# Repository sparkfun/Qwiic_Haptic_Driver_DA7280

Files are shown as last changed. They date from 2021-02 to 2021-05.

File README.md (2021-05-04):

SparkFun Qwiic Haptic Driver - DA7280
========================================

<table class="table table-hover table-striped table-bordered">
  <tr align="center">
   <td><a href="https://www.sparkfun.com/products/17590">*SparkFun Qwiic Haptic Driver - DA7280 (ROB-17590)</a></td>
   <td><a href="https://www.sparkfun.com/products/18247">SparkFun Qwiic Haptic Driver - DA7280 (ROB-18247)</a></td>
  </tr>
  <tr align="center">
   <td><i>SparkFun Qwiic Haptic Driver - DA7280 [<a href="https://www.sparkfun.com/products/17590">ROB-17590</a>]</i></td>
   <td><i>SparkFun Qwiic Haptic Driver Kit - DA7280 [<a href="https://www.sparkfun.com/products/18247">ROB-18247</a>]</i></td>
  </tr>
</table>

The SparkFun Qwiic Haptic Driver includes an itty-bitty, Linear Resonant Actuator (LRA) vibration motor and Dialog Semiconductor's DA7280 motor driver IC for applications that require haptic feedback. The kit is intended for applications where the vibration motor needs to be mounted separately from the board. Please be aware that you will need to manually solder the wires and motor to the board.

Control the vibration motor with the DA7280 via I<sup>2</sup>C, PWM, or a combination of three general purpose input pins. Utilizing our handy Qwiic system, no soldering is required to connect it to the rest of your system. However, we still include 0.1"-spaced PTH pads in case you prefer to use a breadboard to access the driver's I<sup>2</sup>C, power, interrupt, and general purpose input pins on the edge of the board.

This board is great for projects that require a physical indicator whenever an event is triggered. Add it to your remote control to notify you when your robot has hit a wall. Combine it with an accelerometer to remind you to correct your posture. Or use it with a distance sensor to alert you when a ninja is walking up to you at your desk.

Repository Contents
-------------------

* **/Documentation** - Data sheets, additional product information
* **/Hardware** - Eagle design files (.brd, .sch)
* **/Production** - Production panel files (.brd)

Documentation
--------------

* **[Library](https://github.com/sparkfun/DA7280_Haptic_Driver_Arduino_Library)** - Arduino library
* **[Hookup Guide](https://learn.sparkfun.com/tutorials/1461)**

Product Versions
----------------

* [ROB-17590](https://www.sparkfun.com/products/17590)

Version History
---------------

* v1.0 - Initial Release

License Information
-------------------

This product is _**open source**_! 

Please review the LICENSE.md file for license information. 

If you have any questions or concerns on licensing, please contact technical support on our [SparkFun forums](https://forum.sparkfun.com/viewforum.php?f=152).

Distributed as-is; no warranty is given.

- Your friends at SparkFun.

_<COLLABORATION CREDIT>_

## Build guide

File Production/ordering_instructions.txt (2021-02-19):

panel size, 143x192mm
PCB thickness, 1.6mm
number of layers, 2
soldermask color, Red
silkscreen color, White
oz copper, 1oz
finish, HASL lead free
stencils, top
pcs per panel, 30
min trace width, 0.2032mm / 0.0080in
min drill size, 0.3048mm / 0.0120in

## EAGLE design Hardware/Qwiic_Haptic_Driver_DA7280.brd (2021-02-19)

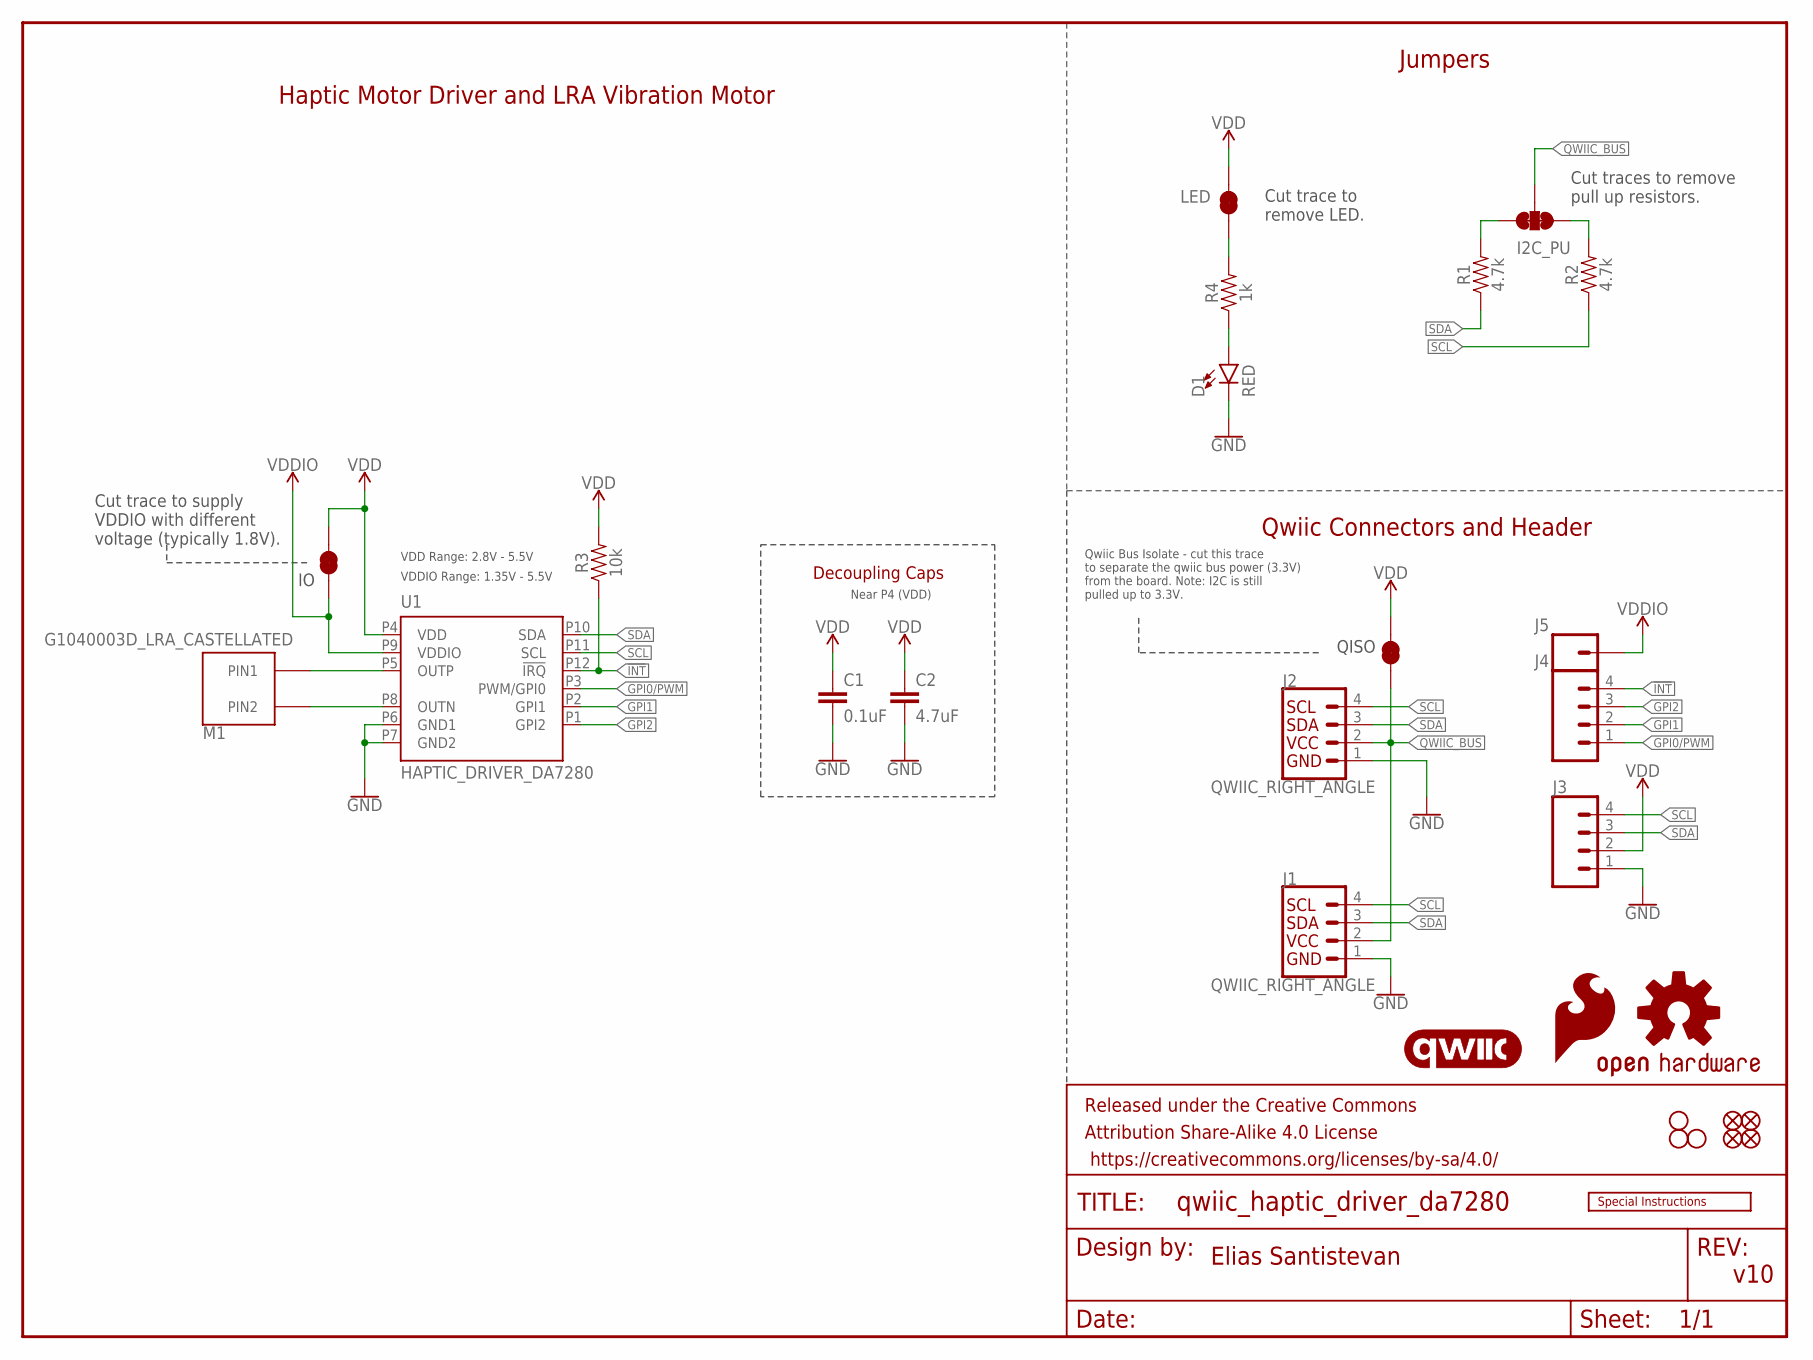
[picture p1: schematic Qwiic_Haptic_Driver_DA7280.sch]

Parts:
C1: 0.1uF; 0603
C2: 4.7uF; 0603
D1: RED; LED-0603
FD1, FD2, FD3, FD4: FIDUCIALUFIDUCIAL; FIDUCIAL-MICRO
FRAME1: FRAME-LETTER; CREATIVE_COMMONS
H1, H2, H4: STAND-OFFTIGHT; STAND-OFF-TIGHT
J1, J2: QWIIC_RIGHT_ANGLE; JST04_1MM_RA
J3, J4: CONN_041X04_NO_SILK_NO_POP; 1X04_NO_SILK
J5: CONN_01PTH_NO_SILK_YES_STOP; 1X01_NO_SILK
JP1, JP2, JP4: LED; SMT-JUMPER_2_NC_TRACE_SILK
JP3: I2C_PU; SMT-JUMPER_3_2-NC_TRACE_SILK
LOGO1: SPECIAL_INSTRUCTIONS-ORDERING; ORDERING_INSTRUCTIONS
LOGO2: OSHW-LOGOS; OSHW-LOGO-S
LOGO4: SFE_LOGO_FLAME.1_INCH; SFE_LOGO_FLAME_.1
M1: G1040003D_LRA_CASTELLATED; COIN_VIBRATION_MOTOR_CASTEL
R1, R2: 4.7k; 0603
R3: 10k; 0603
R4: 1k; 0603
U1: HAPTIC_DRIVER_DA7280; QFN_DA7280
U$1: QWIIC_LOGO_3MM; QWIIC_3MM

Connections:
!INT!: J4.4, R3.1, U1.P12 (!IRQ!)
GND: C1.2, C2.2, D1.C, J1.1, J2.1, J3.1, U1.P6 (GND1), U1.P7 (GND2)
GPI0/PWM: J4.1, U1.P3 (PWM/GPI0)
GPI1: J4.2, U1.P2 (GPI1)
GPI2: J4.3, U1.P1 (GPI2)
unnamed: D1.A, R4.1
unnamed: JP1.1, R4.2
unnamed: JP3.3, R1.2
unnamed: JP3.1, R2.2
unnamed: M1.P$1 (PIN1), U1.P5 (OUTP)
unnamed: M1.P$2 (PIN2), U1.P8 (OUTN)
QWIIC_BUS: J1.2, J2.2, JP3.2, JP4.1
SCL: J1.4, J2.4, J3.4, R2.1, U1.P11 (SCL)
SDA: J1.3, J2.3, J3.3, R1.1, U1.P10 (SDA)
VDD: C1.1, C2.1, J3.2, JP1.2, JP2.2, JP4.2, R3.2, U1.P4 (VDD)
VDDIO: J5.1, JP2.1, U1.P9 (VDDIO)

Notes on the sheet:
v10
Qwiic Connectors and Header
Jumpers
Cut trace to remove LED.
Cut traces to remove pull up resistors.
Haptic Motor Driver and LRA Vibration Motor
Elias Santistevan
Near P4 (VDD)
Decoupling Caps
VDD Range: 2.8V - 5.5V
VDDIO Range: 1.35V - 5.5V
Cut trace to supply VDDIO with different voltage (typically 1.8V).
QISO
Qwiic Bus Isolate - cut this trace to separate the qwiic bus power (3.3V) from the board. Note: I2C is still pulled up to 3.3V.

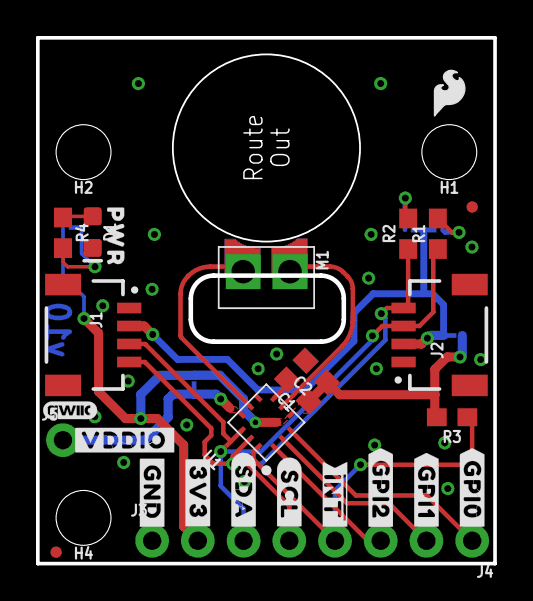
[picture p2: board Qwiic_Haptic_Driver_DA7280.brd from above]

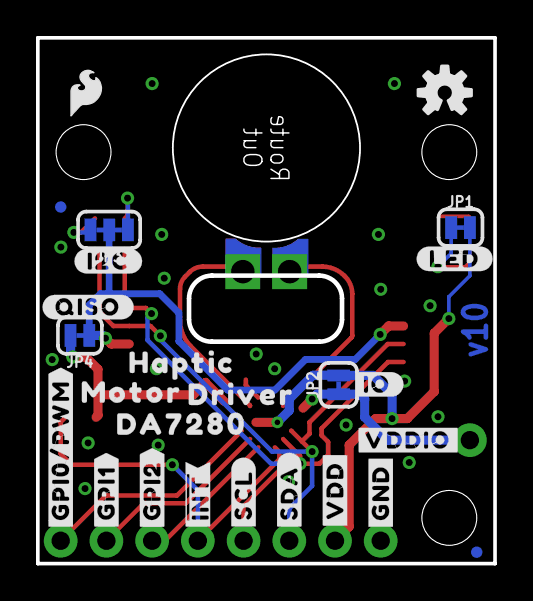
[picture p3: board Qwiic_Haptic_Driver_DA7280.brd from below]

Board: 2 copper layers, 25.4 x 29.2 mm, 58 parts (25 on the bottom side), 16 nets.

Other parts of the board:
U$2: #3V3#1
U$3, U$18: #GND#0
U$4: #GPI0#6
U$5: #GPI1#6
U$6: #GPI2#6
U$7: #VDD#4
U$8: #SDA#4
U$9: HAPTIC6
U$10: MOTOR7
U$11: DRIVER8
U$12: #GPI0#PWM#2
U$13: #GPI1#2
U$14: #GPI2#2
U$15, U$25: #VDDIO#5
U$16: #SDA#0
U$19: #SCL#5
U$20: PWR72810
U$21: #SCL#1
U$23: #I2C#4
U$24: #LED#4
U$26: SFE_LOGO_FLAME_.1
U$27: ##INT##3
U$28: ##INT##6
U$29: DA72809
U$30: #IO#6
U$31: #QISO#0

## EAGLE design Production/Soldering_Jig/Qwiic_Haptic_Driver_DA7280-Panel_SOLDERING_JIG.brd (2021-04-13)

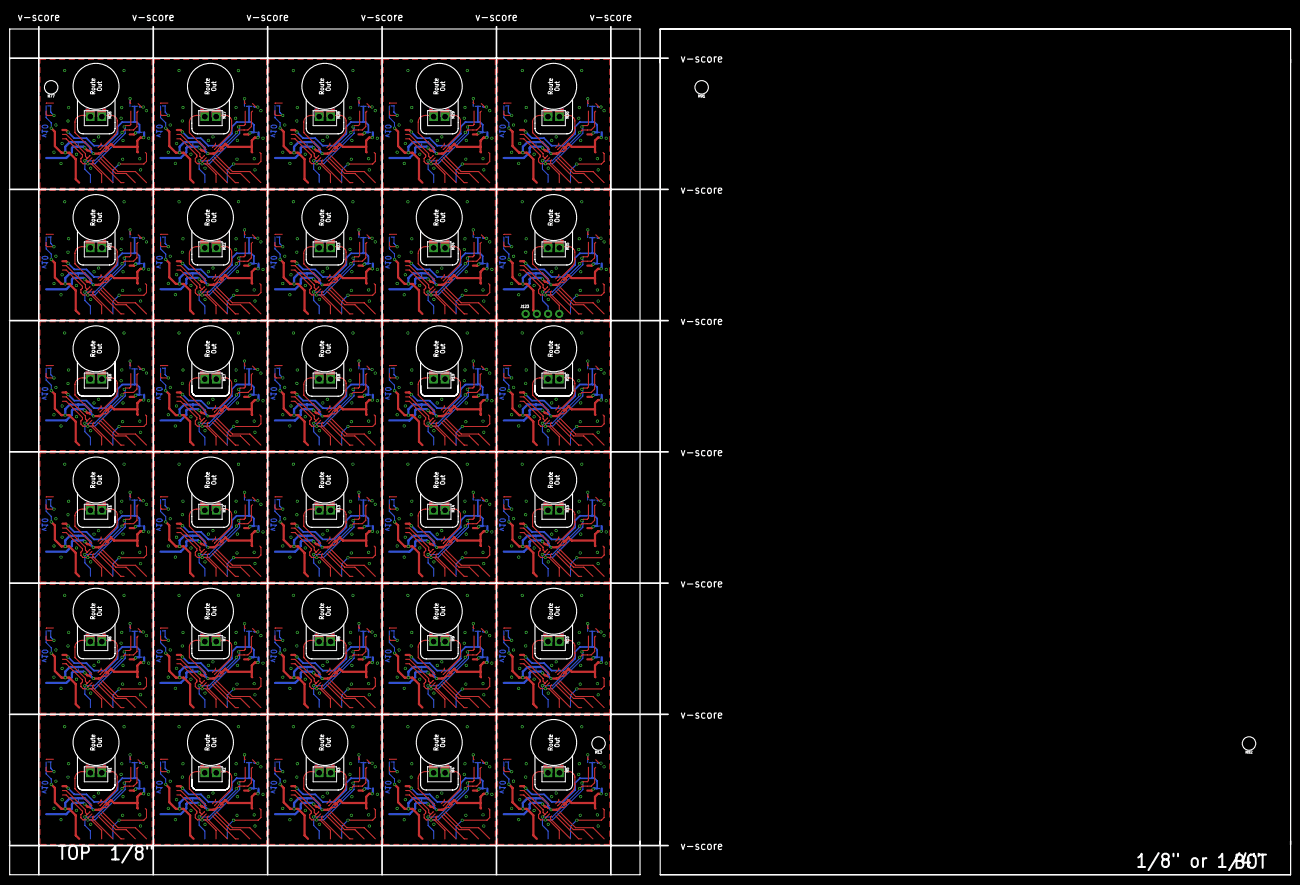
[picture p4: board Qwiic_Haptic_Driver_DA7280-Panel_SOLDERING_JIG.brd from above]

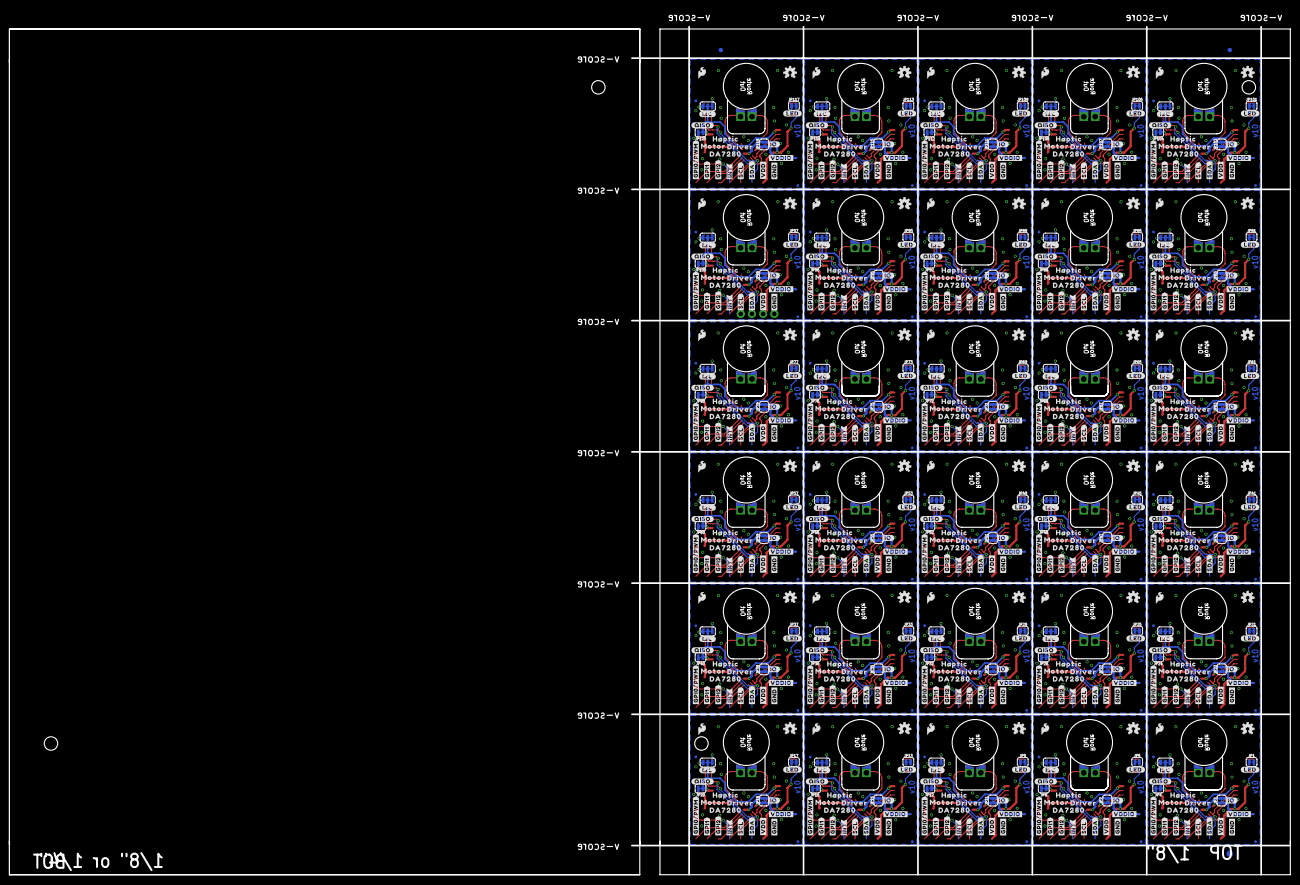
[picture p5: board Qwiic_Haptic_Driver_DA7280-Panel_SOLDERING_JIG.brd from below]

Board: 2 copper layers, 290.1 x 192.0 mm, 788 parts (753 on the bottom side), 60 nets.

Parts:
E$2, E$4: FIDUCIAL-1X2
E$6: FIDUCIAL-1.5X3
FD2, FD4, FD6, FD8, FD10, FD12, FD14, FD16, FD18, FD20, FD22, FD24, FD26, FD28, FD30, FD32, FD34, FD36, FD38, FD40, FD42, FD44, FD46, FD48, FD50, FD52, FD54, FD56, FD58, FD60, FD62, FD64, FD66, FD68, FD70, FD72, FD74, FD76, FD78, FD80, FD82, FD84, FD86, FD88, FD90, FD92, FD94, FD96, FD98, FD100, FD102, FD104, FD106, FD108, FD110, FD112, FD114, FD116, FD118, FD120: FIDUCIALUFIDUCIAL; FIDUCIAL-MICRO
H13, H77, H91, H92: STAND-OFFTIGHT; STAND-OFF-TIGHT
J123: 1X04_NO_SILK
JP1, JP2, JP4, JP5, JP7, JP8, JP9, JP11, JP12, JP13, JP15, JP16, JP17, JP19, JP20, JP21, JP23, JP24, JP25, JP27, JP28, JP29, JP31, JP32, JP33, JP35, JP36, JP37, JP39, JP40, JP41, JP43, JP44, JP45, JP47, JP48, JP49, JP51, JP52, JP53, JP55, JP56, JP57, JP59, JP60, JP61, JP63, JP64, JP65, JP67, JP68, JP69, JP71, JP72, JP73, JP75, JP76, JP77, JP79, JP80, JP81, JP83, JP84, JP85, JP87, JP88, JP89, JP91, JP92, JP93, JP95, JP96, JP97, JP99, JP100, JP101, JP103, JP104, JP105, JP107, JP108, JP109, JP111, JP112, JP113, JP115, JP116, JP117, JP119, JP120: LED; SMT-JUMPER_2_NC_TRACE_SILK
JP3, JP6, JP10, JP14, JP18, JP22, JP26, JP30, JP34, JP38, JP42, JP46, JP50, JP54, JP58, JP62, JP66, JP70, JP74, JP78, JP82, JP86, JP90, JP94, JP98, JP102, JP106, JP110, JP114, JP118: I2C_PU; SMT-JUMPER_3_2-NC_TRACE_SILK
LOGO1, LOGO2, LOGO5, LOGO7, LOGO9, LOGO11, LOGO13, LOGO15, LOGO17, LOGO19, LOGO21, LOGO23, LOGO25, LOGO27, LOGO29, LOGO31, LOGO33, LOGO35, LOGO37, LOGO39, LOGO41, LOGO43, LOGO45, LOGO47, LOGO49, LOGO51, LOGO53, LOGO55, LOGO57, LOGO59: OSHW-LOGOS; OSHW-LOGO-S
M1, M2, M3, M4, M5, M6, M7, M8, M9, M10, M11, M12, M13, M14, M15, M16, M17, M18, M19, M20, M21, M22, M23, M24, M25, M26, M27, M28, M29, M30: G1040003D_LRA_CASTELLATED; COIN_VIBRATION_MOTOR_CASTEL
U$7, U$50, U$79, U$108, U$137, U$166, U$195, U$224, U$253, U$282, U$311, U$340, U$369, U$398, U$427, U$456, U$485, U$514, U$543, U$572, U$601, U$630, U$659, U$688, U$717, U$746, U$775, U$804, U$833, U$862: #VDD#4
U$9, U$53, U$82, U$111, U$140, U$169, U$198, U$227, U$256, U$285, U$314, U$343, U$372, U$401, U$430, U$459, U$488, U$517, U$546, U$575, U$604, U$633, U$662, U$691, U$720, U$749, U$778, U$807, U$836, U$865: HAPTIC6
U$10, U$54, U$83, U$112, U$141, U$170, U$199, U$228, U$257, U$286, U$315, U$344, U$373, U$402, U$431, U$460, U$489, U$518, U$547, U$576, U$605, U$634, U$663, U$692, U$721, U$750, U$779, U$808, U$837, U$866: MOTOR7
U$11, U$55, U$84, U$113, U$142, U$171, U$200, U$229, U$258, U$287, U$316, U$345, U$374, U$403, U$432, U$461, U$490, U$519, U$548, U$577, U$606, U$635, U$664, U$693, U$722, U$751, U$780, U$809, U$838, U$867: DRIVER8
U$12, U$36, U$65, U$94, U$123, U$152, U$181, U$210, U$239, U$268, U$297, U$326, U$355, U$384, U$413, U$442, U$471, U$500, U$529, U$558, U$587, U$616, U$645, U$674, U$703, U$732, U$761, U$790, U$819, U$848: #GPI0#PWM#2
U$13, U$37, U$66, U$95, U$124, U$153, U$182, U$211, U$240, U$269, U$298, U$327, U$356, U$385, U$414, U$443, U$472, U$501, U$530, U$559, U$588, U$617, U$646, U$675, U$704, U$733, U$762, U$791, U$820, U$849: #GPI1#2
U$14, U$38, U$67, U$96, U$125, U$154, U$183, U$212, U$241, U$270, U$299, U$328, U$357, U$386, U$415, U$444, U$473, U$502, U$531, U$560, U$589, U$618, U$647, U$676, U$705, U$734, U$763, U$792, U$821, U$850: #GPI2#2
U$16, U$39, U$68, U$97, U$126, U$155, U$184, U$213, U$242, U$271, U$300, U$329, U$358, U$387, U$416, U$445, U$474, U$503, U$532, U$561, U$590, U$619, U$648, U$677, U$706, U$735, U$764, U$793, U$822, U$851: #SDA#0
U$18, U$40, U$69, U$98, U$127, U$156, U$185, U$214, U$243, U$272, U$301, U$330, U$359, U$388, U$417, U$446, U$475, U$504, U$533, U$562, U$591, U$620, U$649, U$678, U$707, U$736, U$765, U$794, U$823, U$852: #GND#0
U$21, U$43, U$72, U$101, U$130, U$159, U$188, U$217, U$246, U$275, U$304, U$333, U$362, U$391, U$420, U$449, U$478, U$507, U$536, U$565, U$594, U$623, U$652, U$681, U$710, U$739, U$768, U$797, U$826, U$855: #SCL#1
U$23, U$44, U$73, U$102, U$131, U$160, U$189, U$218, U$247, U$276, U$305, U$334, U$363, U$392, U$421, U$450, U$479, U$508, U$537, U$566, U$595, U$624, U$653, U$682, U$711, U$740, U$769, U$798, U$827, U$856: #I2C#4
U$24, U$45, U$74, U$103, U$132, U$161, U$190, U$219, U$248, U$277, U$306, U$335, U$364, U$393, U$422, U$451, U$480, U$509, U$538, U$567, U$596, U$625, U$654, U$683, U$712, U$741, U$770, U$799, U$828, U$857: #LED#4
U$25, U$52, U$81, U$110, U$139, U$168, U$197, U$226, U$255, U$284, U$313, U$342, U$371, U$400, U$429, U$458, U$487, U$516, U$545, U$574, U$603, U$632, U$661, U$690, U$719, U$748, U$777, U$806, U$835, U$864: #VDDIO#5
U$26, U$47, U$76, U$105, U$134, U$163, U$192, U$221, U$250, U$279, U$308, U$337, U$366, U$395, U$424, U$453, U$482, U$511, U$540, U$569, U$598, U$627, U$656, U$685, U$714, U$743, U$772, U$801, U$830, U$859: SFE_LOGO_FLAME_.1
U$27, U$48, U$77, U$106, U$135, U$164, U$193, U$222, U$251, U$280, U$309, U$338, U$367, U$396, U$425, U$454, U$483, U$512, U$541, U$570, U$599, U$628, U$657, U$686, U$715, U$744, U$773, U$802, U$831, U$860: ##INT##3
U$29, U$56, U$85, U$114, U$143, U$172, U$201, U$230, U$259, U$288, U$317, U$346, U$375, U$404, U$433, U$462, U$491, U$520, U$549, U$578, U$607, U$636, U$665, U$694, U$723, U$752, U$781, U$810, U$839, U$868: DA72809
U$30, U$57, U$86, U$115, U$144, U$173, U$202, U$231, U$260, U$289, U$318, U$347, U$376, U$405, U$434, U$463, U$492, U$521, U$550, U$579, U$608, U$637, U$666, U$695, U$724, U$753, U$782, U$811, U$840, U$869: #IO#6
U$31, U$58, U$87, U$116, U$145, U$174, U$203, U$232, U$261, U$290, U$319, U$348, U$377, U$406, U$435, U$464, U$493, U$522, U$551, U$580, U$609, U$638, U$667, U$696, U$725, U$754, U$783, U$812, U$841, U$870: #QISO#0

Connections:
QWIIC_BUS: JP3.2, JP4.1
QWIIC_BUS1: JP6.2, JP8.1
QWIIC_BUS2: JP10.2, JP12.1
QWIIC_BUS3: JP14.2, JP16.1
QWIIC_BUS4: JP18.2, JP20.1
QWIIC_BUS5: JP22.2, JP24.1
QWIIC_BUS6: JP26.2, JP28.1
QWIIC_BUS7: JP30.2, JP32.1
QWIIC_BUS8: JP34.2, JP36.1
QWIIC_BUS9: JP38.2, JP40.1
QWIIC_BUS10: JP42.2, JP44.1
QWIIC_BUS11: JP46.2, JP48.1
QWIIC_BUS12: JP50.2, JP52.1
QWIIC_BUS13: JP54.2, JP56.1
QWIIC_BUS14: JP58.2, JP60.1
QWIIC_BUS15: JP62.2, JP64.1
QWIIC_BUS16: JP66.2, JP68.1
QWIIC_BUS17: JP70.2, JP72.1
QWIIC_BUS18: JP74.2, JP76.1
QWIIC_BUS19: JP78.2, JP80.1
QWIIC_BUS20: JP82.2, JP84.1
QWIIC_BUS21: JP86.2, JP88.1
QWIIC_BUS22: JP90.2, JP92.1
QWIIC_BUS23: JP94.2, JP96.1
QWIIC_BUS24: JP98.2, JP100.1
QWIIC_BUS25: JP102.2, JP104.1
QWIIC_BUS26: JP106.2, JP108.1
QWIIC_BUS27: JP110.2, JP112.1
QWIIC_BUS28: JP114.2, JP116.1
QWIIC_BUS29: JP118.2, JP120.1
VDD: JP1.2, JP2.2, JP4.2
VDD1: JP5.2, JP7.2, JP8.2
VDD2: JP9.2, JP11.2, JP12.2
VDD3: JP13.2, JP15.2, JP16.2
VDD4: JP17.2, JP19.2, JP20.2
VDD5: JP21.2, JP23.2, JP24.2
VDD6: JP25.2, JP27.2, JP28.2
VDD7: JP29.2, JP31.2, JP32.2
VDD8: JP33.2, JP35.2, JP36.2
VDD9: JP37.2, JP39.2, JP40.2
VDD10: JP41.2, JP43.2, JP44.2
VDD11: JP45.2, JP47.2, JP48.2
VDD12: JP49.2, JP51.2, JP52.2
VDD13: JP53.2, JP55.2, JP56.2
VDD14: JP57.2, JP59.2, JP60.2
VDD15: JP61.2, JP63.2, JP64.2
VDD16: JP65.2, JP67.2, JP68.2
VDD17: JP69.2, JP71.2, JP72.2
VDD18: JP73.2, JP75.2, JP76.2
VDD19: JP77.2, JP79.2, JP80.2
VDD20: JP81.2, JP83.2, JP84.2
VDD21: JP85.2, JP87.2, JP88.2
VDD22: JP89.2, JP91.2, JP92.2
VDD23: JP93.2, JP95.2, JP96.2
VDD24: J123.2, JP97.2, JP99.2, JP100.2
VDD25: JP101.2, JP103.2, JP104.2
VDD26: JP105.2, JP107.2, JP108.2
VDD27: JP109.2, JP111.2, JP112.2
VDD28: JP113.2, JP115.2, JP116.2
VDD29: JP117.2, JP119.2, JP120.2

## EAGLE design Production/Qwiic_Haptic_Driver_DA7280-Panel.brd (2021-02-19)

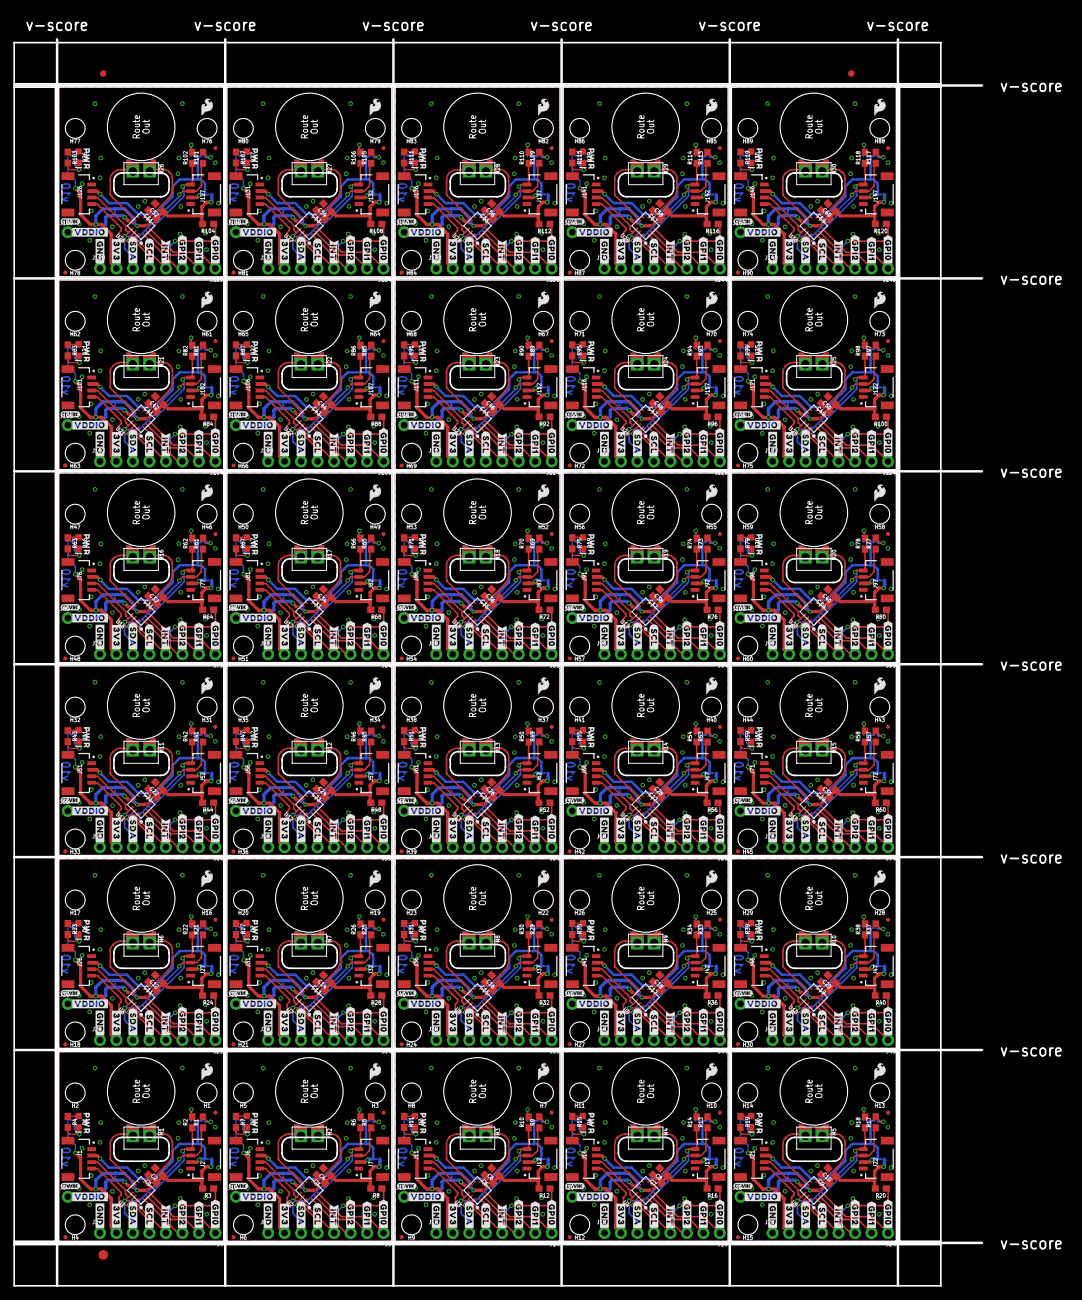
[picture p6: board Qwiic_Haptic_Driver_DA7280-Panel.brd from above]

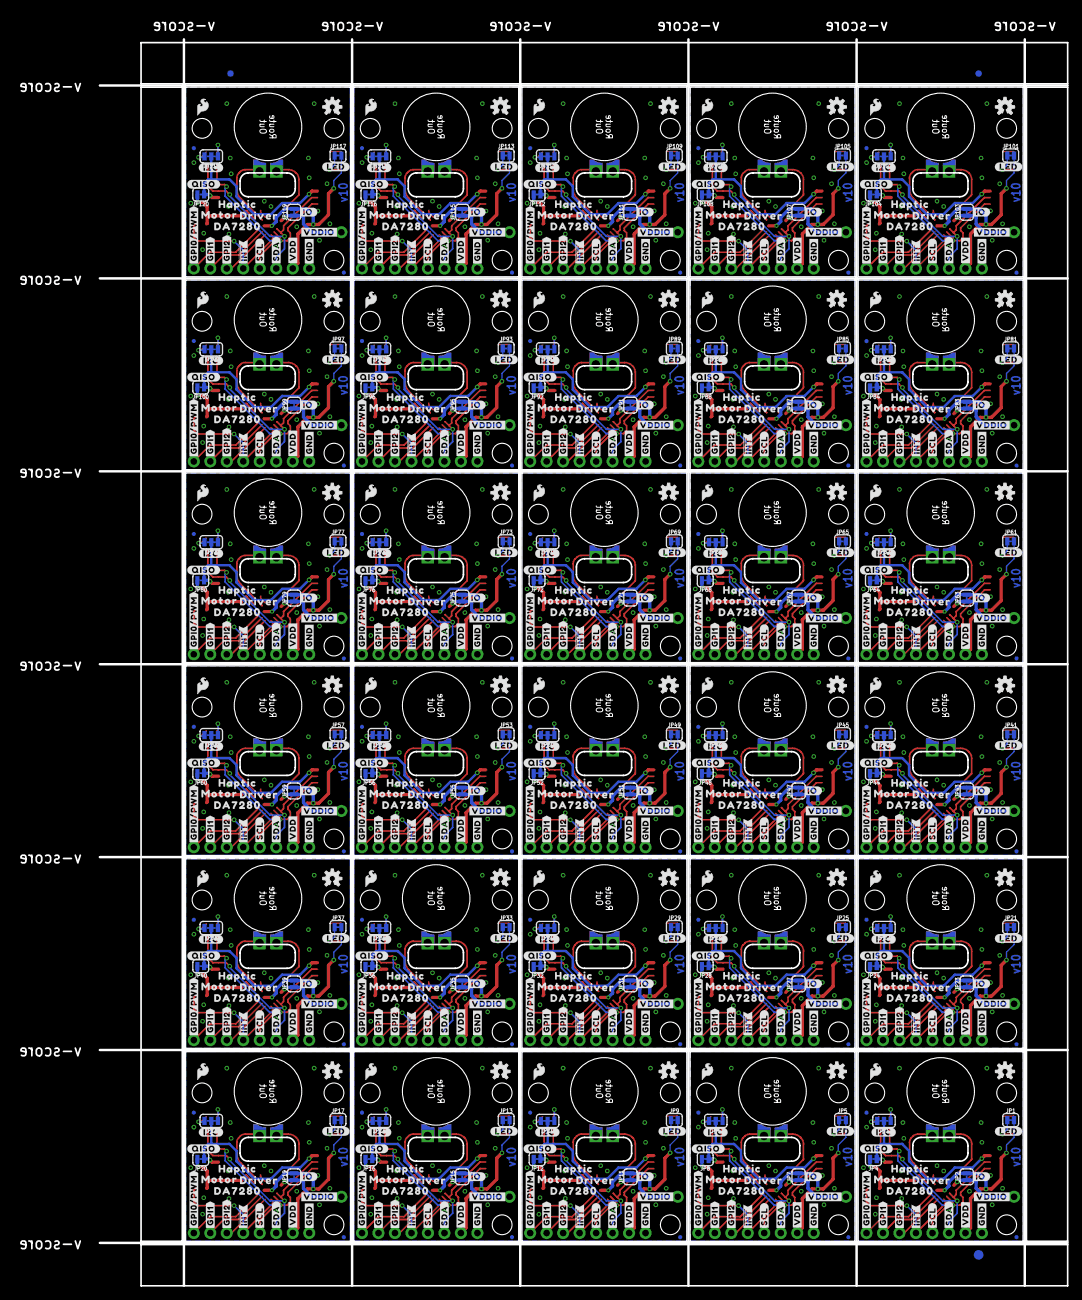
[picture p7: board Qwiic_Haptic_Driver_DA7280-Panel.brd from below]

Board: 2 copper layers, 149.1 x 192.0 mm, 1686 parts (753 on the bottom side), 480 nets.

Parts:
C1, C3, C5, C7, C9, C11, C13, C15, C17, C19, C21, C23, C25, C27, C29, C31, C33, C35, C37, C39, C41, C43, C45, C47, C49, C51, C53, C55, C57, C59: 0.1uF; 0603
C2, C4, C6, C8, C10, C12, C14, C16, C18, C20, C22, C24, C26, C28, C30, C32, C34, C36, C38, C40, C42, C44, C46, C48, C50, C52, C54, C56, C58, C60: 4.7uF; 0603
D1, D2, D3, D4, D5, D6, D7, D8, D9, D10, D11, D12, D13, D14, D15, D16, D17, D18, D19, D20, D21, D22, D23, D24, D25, D26, D27, D28, D29, D30: RED; LED-0603
E$1, E$2, E$3, E$4: FIDUCIAL-1X2
E$5, E$6: FIDUCIAL-1.5X3
FD1, FD2, FD3, FD4, FD5, FD6, FD7, FD8, FD9, FD10, FD11, FD12, FD13, FD14, FD15, FD16, FD17, FD18, FD19, FD20, FD21, FD22, FD23, FD24, FD25, FD26, FD27, FD28, FD29, FD30, FD31, FD32, FD33, FD34, FD35, FD36, FD37, FD38, FD39, FD40, FD41, FD42, FD43, FD44, FD45, FD46, FD47, FD48, FD49, FD50, FD51, FD52, FD53, FD54, FD55, FD56, FD57, FD58, FD59, FD60, FD61, FD62, FD63, FD64, FD65, FD66, FD67, FD68, FD69, FD70, FD71, FD72, FD73, FD74, FD75, FD76, FD77, FD78, FD79, FD80, FD81, FD82, FD83, FD84, FD85, FD86, FD87, FD88, FD89, FD90, FD91, FD92, FD93, FD94, FD95, FD96, FD97, FD98, FD99, FD100, FD101, FD102, FD103, FD104, FD105, FD106, FD107, FD108, FD109, FD110, FD111, FD112, FD113, FD114, FD115, FD116, FD117, FD118, FD119, FD120: FIDUCIALUFIDUCIAL; FIDUCIAL-MICRO
H1, H2, H3, H4, H5, H6, H7, H8, H9, H10, H11, H12, H13, H14, H15, H16, H17, H18, H19, H20, H21, H22, H23, H24, H25, H26, H27, H28, H29, H30, H31, H32, H33, H34, H35, H36, H37, H38, H39, H40, H41, H42, H43, H44, H45, H46, H47, H48, H49, H50, H51, H52, H53, H54, H55, H56, H57, H58, H59, H60, H61, H62, H63, H64, H65, H66, H67, H68, H69, H70, H71, H72, H73, H74, H75, H76, H77, H78, H79, H80, H81, H82, H83, H84, H85, H86, H87, H88, H89, H90: STAND-OFFTIGHT; STAND-OFF-TIGHT
J1, J2, J6, J7, J11, J12, J16, J17, J21, J22, J26, J27, J31, J32, J36, J37, J41, J42, J46, J47, J51, J52, J56, J57, J61, J62, J66, J67, J71, J72, J76, J77, J81, J82, J86, J87, J91, J92, J96, J97, J101, J102, J106, J107, J111, J112, J116, J117, J121, J122, J126, J127, J131, J132, J136, J137, J141, J142, J146, J147: QWIIC_RIGHT_ANGLE; JST04_1MM_RA
J3, J4, J8, J9, J13, J14, J18, J19, J23, J24, J28, J29, J33, J34, J38, J39, J43, J44, J48, J49, J53, J54, J58, J59, J63, J64, J68, J69, J73, J74, J78, J79, J83, J84, J88, J89, J93, J94, J98, J99, J103, J104, J108, J109, J113, J114, J118, J119, J123, J124, J128, J129, J133, J134, J138, J139, J143, J144, J148, J149: 1X04_NO_SILK
J5, J10, J15, J20, J25, J30, J35, J40, J45, J50, J55, J60, J65, J70, J75, J80, J85, J90, J95, J100, J105, J110, J115, J120, J125, J130, J135, J140, J145, J150: 1X01_NO_SILK
JP1, JP2, JP4, JP5, JP7, JP8, JP9, JP11, JP12, JP13, JP15, JP16, JP17, JP19, JP20, JP21, JP23, JP24, JP25, JP27, JP28, JP29, JP31, JP32, JP33, JP35, JP36, JP37, JP39, JP40, JP41, JP43, JP44, JP45, JP47, JP48, JP49, JP51, JP52, JP53, JP55, JP56, JP57, JP59, JP60, JP61, JP63, JP64, JP65, JP67, JP68, JP69, JP71, JP72, JP73, JP75, JP76, JP77, JP79, JP80, JP81, JP83, JP84, JP85, JP87, JP88, JP89, JP91, JP92, JP93, JP95, JP96, JP97, JP99, JP100, JP101, JP103, JP104, JP105, JP107, JP108, JP109, JP111, JP112, JP113, JP115, JP116, JP117, JP119, JP120: LED; SMT-JUMPER_2_NC_TRACE_SILK
JP3, JP6, JP10, JP14, JP18, JP22, JP26, JP30, JP34, JP38, JP42, JP46, JP50, JP54, JP58, JP62, JP66, JP70, JP74, JP78, JP82, JP86, JP90, JP94, JP98, JP102, JP106, JP110, JP114, JP118: I2C_PU; SMT-JUMPER_3_2-NC_TRACE_SILK
LOGO1, LOGO2, LOGO5, LOGO7, LOGO9, LOGO11, LOGO13, LOGO15, LOGO17, LOGO19, LOGO21, LOGO23, LOGO25, LOGO27, LOGO29, LOGO31, LOGO33, LOGO35, LOGO37, LOGO39, LOGO41, LOGO43, LOGO45, LOGO47, LOGO49, LOGO51, LOGO53, LOGO55, LOGO57, LOGO59: OSHW-LOGOS; OSHW-LOGO-S
LOGO3, LOGO4, LOGO6, LOGO8, LOGO10, LOGO12, LOGO14, LOGO16, LOGO18, LOGO20, LOGO22, LOGO24, LOGO26, LOGO28, LOGO30, LOGO32, LOGO34, LOGO36, LOGO38, LOGO40, LOGO42, LOGO44, LOGO46, LOGO48, LOGO50, LOGO52, LOGO54, LOGO56, LOGO58, LOGO60: SFE_LOGO_FLAME.1_INCH; SFE_LOGO_FLAME_.1
M1, M2, M3, M4, M5, M6, M7, M8, M9, M10, M11, M12, M13, M14, M15, M16, M17, M18, M19, M20, M21, M22, M23, M24, M25, M26, M27, M28, M29, M30: G1040003D_LRA_CASTELLATED; COIN_VIBRATION_MOTOR_CASTEL
R1, R2, R5, R6, R9, R10, R13, R14, R17, R18, R21, R22, R25, R26, R29, R30, R33, R34, R37, R38, R41, R42, R45, R46, R49, R50, R53, R54, R57, R58, R61, R62, R65, R66, R69, R70, R73, R74, R77, R78, R81, R82, R85, R86, R89, R90, R93, R94, R97, R98, R101, R102, R105, R106, R109, R110, R113, R114, R117, R118: 4.7k; 0603
R3, R8, R12, R16, R20, R24, R28, R32, R36, R40, R44, R48, R52, R56, R60, R64, R68, R72, R76, R80, R84, R88, R92, R96, R100, R104, R108, R112, R116, R120: 10k; 0603
R4, R7, R11, R15, R19, R23, R27, R31, R35, R39, R43, R47, R51, R55, R59, R63, R67, R71, R75, R79, R83, R87, R91, R95, R99, R103, R107, R111, R115, R119: 1k; 0603
U1, U2, U3, U4, U5, U6, U7, U8, U9, U10, U11, U12, U13, U14, U15, U16, U17, U18, U19, U20, U21, U22, U23, U24, U25, U26, U27, U28, U29, U30: HAPTIC_DRIVER_DA7280; QFN_DA7280
U$1, U$17, U$59, U$88, U$117, U$146, U$175, U$204, U$233, U$262, U$291, U$320, U$349, U$378, U$407, U$436, U$465, U$494, U$523, U$552, U$581, U$610, U$639, U$668, U$697, U$726, U$755, U$784, U$813, U$842: QWIIC_LOGO_3MM; QWIIC_3MM
U$2, U$46, U$75, U$104, U$133, U$162, U$191, U$220, U$249, U$278, U$307, U$336, U$365, U$394, U$423, U$452, U$481, U$510, U$539, U$568, U$597, U$626, U$655, U$684, U$713, U$742, U$771, U$800, U$829, U$858: #3V3#1
U$3, U$18, U$22, U$40, U$60, U$69, U$89, U$98, U$118, U$127, U$147, U$156, U$176, U$185, U$205, U$214, U$234, U$243, U$263, U$272, U$292, U$301, U$321, U$330, U$350, U$359, U$379, U$388, U$408, U$417, U$437, U$446, U$466, U$475, U$495, U$504, U$524, U$533, U$553, U$562, U$582, U$591, U$611, U$620, U$640, U$649, U$669, U$678, U$698, U$707, U$727, U$736, U$756, U$765, U$785, U$794, U$814, U$823, U$843, U$852: #GND#0
U$4, U$32, U$61, U$90, U$119, U$148, U$177, U$206, U$235, U$264, U$293, U$322, U$351, U$380, U$409, U$438, U$467, U$496, U$525, U$554, U$583, U$612, U$641, U$670, U$699, U$728, U$757, U$786, U$815, U$844: #GPI0#6
U$5, U$33, U$62, U$91, U$120, U$149, U$178, U$207, U$236, U$265, U$294, U$323, U$352, U$381, U$410, U$439, U$468, U$497, U$526, U$555, U$584, U$613, U$642, U$671, U$700, U$729, U$758, U$787, U$816, U$845: #GPI1#6
U$6, U$34, U$63, U$92, U$121, U$150, U$179, U$208, U$237, U$266, U$295, U$324, U$353, U$382, U$411, U$440, U$469, U$498, U$527, U$556, U$585, U$614, U$643, U$672, U$701, U$730, U$759, U$788, U$817, U$846: #GPI2#6
U$7, U$50, U$79, U$108, U$137, U$166, U$195, U$224, U$253, U$282, U$311, U$340, U$369, U$398, U$427, U$456, U$485, U$514, U$543, U$572, U$601, U$630, U$659, U$688, U$717, U$746, U$775, U$804, U$833, U$862: #VDD#4
U$8, U$35, U$64, U$93, U$122, U$151, U$180, U$209, U$238, U$267, U$296, U$325, U$354, U$383, U$412, U$441, U$470, U$499, U$528, U$557, U$586, U$615, U$644, U$673, U$702, U$731, U$760, U$789, U$818, U$847: #SDA#4
U$9, U$53, U$82, U$111, U$140, U$169, U$198, U$227, U$256, U$285, U$314, U$343, U$372, U$401, U$430, U$459, U$488, U$517, U$546, U$575, U$604, U$633, U$662, U$691, U$720, U$749, U$778, U$807, U$836, U$865: HAPTIC6
U$10, U$54, U$83, U$112, U$141, U$170, U$199, U$228, U$257, U$286, U$315, U$344, U$373, U$402, U$431, U$460, U$489, U$518, U$547, U$576, U$605, U$634, U$663, U$692, U$721, U$750, U$779, U$808, U$837, U$866: MOTOR7
U$11, U$55, U$84, U$113, U$142, U$171, U$200, U$229, U$258, U$287, U$316, U$345, U$374, U$403, U$432, U$461, U$490, U$519, U$548, U$577, U$606, U$635, U$664, U$693, U$722, U$751, U$780, U$809, U$838, U$867: DRIVER8
U$12, U$36, U$65, U$94, U$123, U$152, U$181, U$210, U$239, U$268, U$297, U$326, U$355, U$384, U$413, U$442, U$471, U$500, U$529, U$558, U$587, U$616, U$645, U$674, U$703, U$732, U$761, U$790, U$819, U$848: #GPI0#PWM#2
U$13, U$37, U$66, U$95, U$124, U$153, U$182, U$211, U$240, U$269, U$298, U$327, U$356, U$385, U$414, U$443, U$472, U$501, U$530, U$559, U$588, U$617, U$646, U$675, U$704, U$733, U$762, U$791, U$820, U$849: #GPI1#2
U$14, U$38, U$67, U$96, U$125, U$154, U$183, U$212, U$241, U$270, U$299, U$328, U$357, U$386, U$415, U$444, U$473, U$502, U$531, U$560, U$589, U$618, U$647, U$676, U$705, U$734, U$763, U$792, U$821, U$850: #GPI2#2
U$15, U$25, U$51, U$52, U$80, U$81, U$109, U$110, U$138, U$139, U$167, U$168, U$196, U$197, U$225, U$226, U$254, U$255, U$283, U$284, U$312, U$313, U$341, U$342, U$370, U$371, U$399, U$400, U$428, U$429, U$457, U$458, U$486, U$487, U$515, U$516, U$544, U$545, U$573, U$574, U$602, U$603, U$631, U$632, U$660, U$661, U$689, U$690, U$718, U$719, U$747, U$748, U$776, U$777, U$805, U$806, U$834, U$835, U$863, U$864: #VDDIO#5
U$16, U$39, U$68, U$97, U$126, U$155, U$184, U$213, U$242, U$271, U$300, U$329, U$358, U$387, U$416, U$445, U$474, U$503, U$532, U$561, U$590, U$619, U$648, U$677, U$706, U$735, U$764, U$793, U$822, U$851: #SDA#0
U$19, U$41, U$70, U$99, U$128, U$157, U$186, U$215, U$244, U$273, U$302, U$331, U$360, U$389, U$418, U$447, U$476, U$505, U$534, U$563, U$592, U$621, U$650, U$679, U$708, U$737, U$766, U$795, U$824, U$853: #SCL#5
U$20, U$42, U$71, U$100, U$129, U$158, U$187, U$216, U$245, U$274, U$303, U$332, U$361, U$390, U$419, U$448, U$477, U$506, U$535, U$564, U$593, U$622, U$651, U$680, U$709, U$738, U$767, U$796, U$825, U$854: PWR72810
U$21, U$43, U$72, U$101, U$130, U$159, U$188, U$217, U$246, U$275, U$304, U$333, U$362, U$391, U$420, U$449, U$478, U$507, U$536, U$565, U$594, U$623, U$652, U$681, U$710, U$739, U$768, U$797, U$826, U$855: #SCL#1
U$23, U$44, U$73, U$102, U$131, U$160, U$189, U$218, U$247, U$276, U$305, U$334, U$363, U$392, U$421, U$450, U$479, U$508, U$537, U$566, U$595, U$624, U$653, U$682, U$711, U$740, U$769, U$798, U$827, U$856: #I2C#4
U$24, U$45, U$74, U$103, U$132, U$161, U$190, U$219, U$248, U$277, U$306, U$335, U$364, U$393, U$422, U$451, U$480, U$509, U$538, U$567, U$596, U$625, U$654, U$683, U$712, U$741, U$770, U$799, U$828, U$857: #LED#4
U$26, U$47, U$76, U$105, U$134, U$163, U$192, U$221, U$250, U$279, U$308, U$337, U$366, U$395, U$424, U$453, U$482, U$511, U$540, U$569, U$598, U$627, U$656, U$685, U$714, U$743, U$772, U$801, U$830, U$859: SFE_LOGO_FLAME_.1
U$27, U$48, U$77, U$106, U$135, U$164, U$193, U$222, U$251, U$280, U$309, U$338, U$367, U$396, U$425, U$454, U$483, U$512, U$541, U$570, U$599, U$628, U$657, U$686, U$715, U$744, U$773, U$802, U$831, U$860: ##INT##3
U$28, U$49, U$78, U$107, U$136, U$165, U$194, U$223, U$252, U$281, U$310, U$339, U$368, U$397, U$426, U$455, U$484, U$513, U$542, U$571, U$600, U$629, U$658, U$687, U$716, U$745, U$774, U$803, U$832, U$861: ##INT##6
U$29, U$56, U$85, U$114, U$143, U$172, U$201, U$230, U$259, U$288, U$317, U$346, U$375, U$404, U$433, U$462, U$491, U$520, U$549, U$578, U$607, U$636, U$665, U$694, U$723, U$752, U$781, U$810, U$839, U$868: DA72809
U$30, U$57, U$86, U$115, U$144, U$173, U$202, U$231, U$260, U$289, U$318, U$347, U$376, U$405, U$434, U$463, U$492, U$521, U$550, U$579, U$608, U$637, U$666, U$695, U$724, U$753, U$782, U$811, U$840, U$869: #IO#6
U$31, U$58, U$87, U$116, U$145, U$174, U$203, U$232, U$261, U$290, U$319, U$348, U$377, U$406, U$435, U$464, U$493, U$522, U$551, U$580, U$609, U$638, U$667, U$696, U$725, U$754, U$783, U$812, U$841, U$870: #QISO#0

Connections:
!INT!: J4.4, R3.1, U1.P12
!INT!1: J9.4, R8.1, U2.P12
!INT!2: J14.4, R12.1, U3.P12
!INT!3: J19.4, R16.1, U4.P12
!INT!4: J24.4, R20.1, U5.P12
!INT!5: J29.4, R24.1, U6.P12
!INT!6: J34.4, R28.1, U7.P12
!INT!7: J39.4, R32.1, U8.P12
!INT!8: J44.4, R36.1, U9.P12
!INT!9: J49.4, R40.1, U10.P12
!INT!10: J54.4, R44.1, U11.P12
!INT!11: J59.4, R48.1, U12.P12
!INT!12: J64.4, R52.1, U13.P12
!INT!13: J69.4, R56.1, U14.P12
!INT!14: J74.4, R60.1, U15.P12
!INT!15: J79.4, R64.1, U16.P12
!INT!16: J84.4, R68.1, U17.P12
!INT!17: J89.4, R72.1, U18.P12
!INT!18: J94.4, R76.1, U19.P12
!INT!19: J99.4, R80.1, U20.P12
!INT!20: J104.4, R84.1, U21.P12
!INT!21: J109.4, R88.1, U22.P12
!INT!22: J114.4, R92.1, U23.P12
!INT!23: J119.4, R96.1, U24.P12
!INT!24: J124.4, R100.1, U25.P12
!INT!25: J129.4, R104.1, U26.P12
!INT!26: J134.4, R108.1, U27.P12
!INT!27: J139.4, R112.1, U28.P12
!INT!28: J144.4, R116.1, U29.P12
!INT!29: J149.4, R120.1, U30.P12
GND: C1.2, C2.2, D1.C, J1.1, J2.1, J3.1, U1.P6, U1.P7
GND1: C3.2, C4.2, D2.C, J6.1, J7.1, J8.1, U2.P6, U2.P7
GND2: C5.2, C6.2, D3.C, J11.1, J12.1, J13.1, U3.P6, U3.P7
GND3: C7.2, C8.2, D4.C, J16.1, J17.1, J18.1, U4.P6, U4.P7
GND4: C9.2, C10.2, D5.C, J21.1, J22.1, J23.1, U5.P6, U5.P7
GND5: C11.2, C12.2, D6.C, J26.1, J27.1, J28.1, U6.P6, U6.P7
GND6: C13.2, C14.2, D7.C, J31.1, J32.1, J33.1, U7.P6, U7.P7
GND7: C15.2, C16.2, D8.C, J36.1, J37.1, J38.1, U8.P6, U8.P7
GND8: C17.2, C18.2, D9.C, J41.1, J42.1, J43.1, U9.P6, U9.P7
GND9: C19.2, C20.2, D10.C, J46.1, J47.1, J48.1, U10.P6, U10.P7
GND10: C21.2, C22.2, D11.C, J51.1, J52.1, J53.1, U11.P6, U11.P7
GND11: C23.2, C24.2, D12.C, J56.1, J57.1, J58.1, U12.P6, U12.P7
GND12: C25.2, C26.2, D13.C, J61.1, J62.1, J63.1, U13.P6, U13.P7
GND13: C27.2, C28.2, D14.C, J66.1, J67.1, J68.1, U14.P6, U14.P7
GND14: C29.2, C30.2, D15.C, J71.1, J72.1, J73.1, U15.P6, U15.P7
GND15: C31.2, C32.2, D16.C, J76.1, J77.1, J78.1, U16.P6, U16.P7
GND16: C33.2, C34.2, D17.C, J81.1, J82.1, J83.1, U17.P6, U17.P7
GND17: C35.2, C36.2, D18.C, J86.1, J87.1, J88.1, U18.P6, U18.P7
GND18: C37.2, C38.2, D19.C, J91.1, J92.1, J93.1, U19.P6, U19.P7
GND19: C39.2, C40.2, D20.C, J96.1, J97.1, J98.1, U20.P6, U20.P7
GND20: C41.2, C42.2, D21.C, J101.1, J102.1, J103.1, U21.P6, U21.P7
GND21: C43.2, C44.2, D22.C, J106.1, J107.1, J108.1, U22.P6, U22.P7
GND22: C45.2, C46.2, D23.C, J111.1, J112.1, J113.1, U23.P6, U23.P7
GND23: C47.2, C48.2, D24.C, J116.1, J117.1, J118.1, U24.P6, U24.P7
GND24: C49.2, C50.2, D25.C, J121.1, J122.1, J123.1, U25.P6, U25.P7
GND25: C51.2, C52.2, D26.C, J126.1, J127.1, J128.1, U26.P6, U26.P7
GND26: C53.2, C54.2, D27.C, J131.1, J132.1, J133.1, U27.P6, U27.P7
GND27: C55.2, C56.2, D28.C, J136.1, J137.1, J138.1, U28.P6, U28.P7
GND28: C57.2, C58.2, D29.C, J141.1, J142.1, J143.1, U29.P6, U29.P7
GND29: C59.2, C60.2, D30.C, J146.1, J147.1, J148.1, U30.P6, U30.P7
GPI0/PWM: J4.1, U1.P3
GPI0/PWM1: J9.1, U2.P3
GPI0/PWM2: J14.1, U3.P3
GPI0/PWM3: J19.1, U4.P3
GPI0/PWM4: J24.1, U5.P3
GPI0/PWM5: J29.1, U6.P3
GPI0/PWM6: J34.1, U7.P3
GPI0/PWM7: J39.1, U8.P3
GPI0/PWM8: J44.1, U9.P3
GPI0/PWM9: J49.1, U10.P3
GPI0/PWM10: J54.1, U11.P3
GPI0/PWM11: J59.1, U12.P3
GPI0/PWM12: J64.1, U13.P3
GPI0/PWM13: J69.1, U14.P3
GPI0/PWM14: J74.1, U15.P3
GPI0/PWM15: J79.1, U16.P3
GPI0/PWM16: J84.1, U17.P3
GPI0/PWM17: J89.1, U18.P3
GPI0/PWM18: J94.1, U19.P3
GPI0/PWM19: J99.1, U20.P3
GPI0/PWM20: J104.1, U21.P3
GPI0/PWM21: J109.1, U22.P3
GPI0/PWM22: J114.1, U23.P3
GPI0/PWM23: J119.1, U24.P3
GPI0/PWM24: J124.1, U25.P3
GPI0/PWM25: J129.1, U26.P3
GPI0/PWM26: J134.1, U27.P3
GPI0/PWM27: J139.1, U28.P3
GPI0/PWM28: J144.1, U29.P3
GPI0/PWM29: J149.1, U30.P3
GPI1: J4.2, U1.P2
GPI2: J4.3, U1.P1
GPI3: J9.2, U2.P2
GPI4: J9.3, U2.P1
GPI5: J14.2, U3.P2
GPI6: J14.3, U3.P1
GPI7: J19.2, U4.P2
GPI8: J19.3, U4.P1
GPI9: J24.2, U5.P2
GPI10: J24.3, U5.P1
GPI11: J29.2, U6.P2
GPI12: J29.3, U6.P1
GPI13: J34.2, U7.P2
GPI14: J34.3, U7.P1
GPI15: J39.2, U8.P2
GPI16: J39.3, U8.P1
GPI17: J44.2, U9.P2
GPI18: J44.3, U9.P1
GPI19: J49.2, U10.P2
GPI20: J49.3, U10.P1
GPI21: J54.2, U11.P2
GPI22: J54.3, U11.P1
GPI23: J59.2, U12.P2
GPI24: J59.3, U12.P1
GPI25: J64.2, U13.P2
GPI26: J64.3, U13.P1
GPI27: J69.2, U14.P2
GPI28: J69.3, U14.P1
GPI29: J74.2, U15.P2
GPI30: J74.3, U15.P1
GPI31: J79.2, U16.P2
GPI32: J79.3, U16.P1
GPI33: J84.2, U17.P2
GPI34: J84.3, U17.P1
GPI35: J89.2, U18.P2
GPI36: J89.3, U18.P1
GPI37: J94.2, U19.P2
GPI38: J94.3, U19.P1
GPI39: J99.2, U20.P2
GPI40: J99.3, U20.P1
GPI41: J104.2, U21.P2
GPI42: J104.3, U21.P1
GPI43: J109.2, U22.P2
GPI44: J109.3, U22.P1
GPI45: J114.2, U23.P2
GPI46: J114.3, U23.P1
GPI47: J119.2, U24.P2
GPI48: J119.3, U24.P1
GPI49: J124.2, U25.P2
GPI50: J124.3, U25.P1
GPI51: J129.2, U26.P2
GPI52: J129.3, U26.P1
GPI53: J134.2, U27.P2
GPI54: J134.3, U27.P1
GPI55: J139.2, U28.P2
GPI56: J139.3, U28.P1
GPI57: J144.2, U29.P2
GPI58: J144.3, U29.P1
GPI59: J149.2, U30.P2
GPI60: J149.3, U30.P1
unnamed: D1.A, R4.1
unnamed: JP1.1, R4.2
unnamed: JP3.3, R1.2
unnamed: JP3.1, R2.2
unnamed: M1.P$1, U1.P5
unnamed: M1.P$2, U1.P8
unnamed: D2.A, R7.1
unnamed: JP5.1, R7.2
unnamed: JP6.3, R5.2
unnamed: JP6.1, R6.2
unnamed: M2.P$1, U2.P5
unnamed: M2.P$2, U2.P8
unnamed: D3.A, R11.1
unnamed: JP9.1, R11.2
unnamed: JP10.3, R9.2
unnamed: JP10.1, R10.2
unnamed: M3.P$1, U3.P5
unnamed: M3.P$2, U3.P8
unnamed: D4.A, R15.1
unnamed: JP13.1, R15.2
unnamed: JP14.3, R13.2
unnamed: JP14.1, R14.2
unnamed: M4.P$1, U4.P5
unnamed: M4.P$2, U4.P8
unnamed: D5.A, R19.1
unnamed: JP17.1, R19.2
unnamed: JP18.3, R17.2
unnamed: JP18.1, R18.2
unnamed: M5.P$1, U5.P5
unnamed: M5.P$2, U5.P8
unnamed: D6.A, R23.1
unnamed: JP21.1, R23.2
unnamed: JP22.3, R21.2
unnamed: JP22.1, R22.2
unnamed: M6.P$1, U6.P5
unnamed: M6.P$2, U6.P8
unnamed: D7.A, R27.1
unnamed: JP25.1, R27.2
unnamed: JP26.3, R25.2
unnamed: JP26.1, R26.2
unnamed: M7.P$1, U7.P5
unnamed: M7.P$2, U7.P8
unnamed: D8.A, R31.1
unnamed: JP29.1, R31.2
unnamed: JP30.3, R29.2
unnamed: JP30.1, R30.2
unnamed: M8.P$1, U8.P5
unnamed: M8.P$2, U8.P8
unnamed: D9.A, R35.1
unnamed: JP33.1, R35.2
unnamed: JP34.3, R33.2
unnamed: JP34.1, R34.2
unnamed: M9.P$1, U9.P5
unnamed: M9.P$2, U9.P8
unnamed: D10.A, R39.1
unnamed: JP37.1, R39.2
unnamed: JP38.3, R37.2
unnamed: JP38.1, R38.2
unnamed: M10.P$1, U10.P5
unnamed: M10.P$2, U10.P8
unnamed: D11.A, R43.1
unnamed: JP41.1, R43.2
unnamed: JP42.3, R41.2
unnamed: JP42.1, R42.2
unnamed: M11.P$1, U11.P5
unnamed: M11.P$2, U11.P8
unnamed: D12.A, R47.1
unnamed: JP45.1, R47.2
unnamed: JP46.3, R45.2
unnamed: JP46.1, R46.2
unnamed: M12.P$1, U12.P5
unnamed: M12.P$2, U12.P8
unnamed: D13.A, R51.1
unnamed: JP49.1, R51.2
unnamed: JP50.3, R49.2
unnamed: JP50.1, R50.2
unnamed: M13.P$1, U13.P5
unnamed: M13.P$2, U13.P8
unnamed: D14.A, R55.1
unnamed: JP53.1, R55.2
unnamed: JP54.3, R53.2
unnamed: JP54.1, R54.2
unnamed: M14.P$1, U14.P5
unnamed: M14.P$2, U14.P8
unnamed: D15.A, R59.1
unnamed: JP57.1, R59.2
unnamed: JP58.3, R57.2
unnamed: JP58.1, R58.2
unnamed: M15.P$1, U15.P5
unnamed: M15.P$2, U15.P8
unnamed: D16.A, R63.1
unnamed: JP61.1, R63.2
unnamed: JP62.3, R61.2
unnamed: JP62.1, R62.2
unnamed: M16.P$1, U16.P5
unnamed: M16.P$2, U16.P8
unnamed: D17.A, R67.1
unnamed: JP65.1, R67.2
unnamed: JP66.3, R65.2
unnamed: JP66.1, R66.2
unnamed: M17.P$1, U17.P5
unnamed: M17.P$2, U17.P8
unnamed: D18.A, R71.1
unnamed: JP69.1, R71.2
unnamed: JP70.3, R69.2
unnamed: JP70.1, R70.2
unnamed: M18.P$1, U18.P5
unnamed: M18.P$2, U18.P8
unnamed: D19.A, R75.1
unnamed: JP73.1, R75.2
unnamed: JP74.3, R73.2
unnamed: JP74.1, R74.2
unnamed: M19.P$1, U19.P5
unnamed: M19.P$2, U19.P8
unnamed: D20.A, R79.1
unnamed: JP77.1, R79.2
unnamed: JP78.3, R77.2
unnamed: JP78.1, R78.2
unnamed: M20.P$1, U20.P5
unnamed: M20.P$2, U20.P8
unnamed: D21.A, R83.1
unnamed: JP81.1, R83.2
unnamed: JP82.3, R81.2
unnamed: JP82.1, R82.2
unnamed: M21.P$1, U21.P5
unnamed: M21.P$2, U21.P8
unnamed: D22.A, R87.1
unnamed: JP85.1, R87.2
unnamed: JP86.3, R85.2
unnamed: JP86.1, R86.2
unnamed: M22.P$1, U22.P5
unnamed: M22.P$2, U22.P8
unnamed: D23.A, R91.1
unnamed: JP89.1, R91.2
unnamed: JP90.3, R89.2
unnamed: JP90.1, R90.2
unnamed: M23.P$1, U23.P5
unnamed: M23.P$2, U23.P8
unnamed: D24.A, R95.1
unnamed: JP93.1, R95.2
unnamed: JP94.3, R93.2
unnamed: JP94.1, R94.2
unnamed: M24.P$1, U24.P5
unnamed: M24.P$2, U24.P8
unnamed: D25.A, R99.1
unnamed: JP97.1, R99.2
unnamed: JP98.3, R97.2
unnamed: JP98.1, R98.2
unnamed: M25.P$1, U25.P5
unnamed: M25.P$2, U25.P8
unnamed: D26.A, R103.1
unnamed: JP101.1, R103.2
unnamed: JP102.3, R101.2
unnamed: JP102.1, R102.2
unnamed: M26.P$1, U26.P5
unnamed: M26.P$2, U26.P8
unnamed: D27.A, R107.1
unnamed: JP105.1, R107.2
unnamed: JP106.3, R105.2
unnamed: JP106.1, R106.2
unnamed: M27.P$1, U27.P5
unnamed: M27.P$2, U27.P8
unnamed: D28.A, R111.1
unnamed: JP109.1, R111.2
unnamed: JP110.3, R109.2
unnamed: JP110.1, R110.2
unnamed: M28.P$1, U28.P5
unnamed: M28.P$2, U28.P8
unnamed: D29.A, R115.1
unnamed: JP113.1, R115.2
unnamed: JP114.3, R113.2
unnamed: JP114.1, R114.2
unnamed: M29.P$1, U29.P5
unnamed: M29.P$2, U29.P8
unnamed: D30.A, R119.1
unnamed: JP117.1, R119.2
unnamed: JP118.3, R117.2
unnamed: JP118.1, R118.2
unnamed: M30.P$1, U30.P5
unnamed: M30.P$2, U30.P8
QWIIC_BUS: J1.2, J2.2, JP3.2, JP4.1
QWIIC_BUS1: J6.2, J7.2, JP6.2, JP8.1
QWIIC_BUS2: J11.2, J12.2, JP10.2, JP12.1
QWIIC_BUS3: J16.2, J17.2, JP14.2, JP16.1
QWIIC_BUS4: J21.2, J22.2, JP18.2, JP20.1
QWIIC_BUS5: J26.2, J27.2, JP22.2, JP24.1
QWIIC_BUS6: J31.2, J32.2, JP26.2, JP28.1
QWIIC_BUS7: J36.2, J37.2, JP30.2, JP32.1
QWIIC_BUS8: J41.2, J42.2, JP34.2, JP36.1
QWIIC_BUS9: J46.2, J47.2, JP38.2, JP40.1
QWIIC_BUS10: J51.2, J52.2, JP42.2, JP44.1
QWIIC_BUS11: J56.2, J57.2, JP46.2, JP48.1
QWIIC_BUS12: J61.2, J62.2, JP50.2, JP52.1
QWIIC_BUS13: J66.2, J67.2, JP54.2, JP56.1
QWIIC_BUS14: J71.2, J72.2, JP58.2, JP60.1
QWIIC_BUS15: J76.2, J77.2, JP62.2, JP64.1
QWIIC_BUS16: J81.2, J82.2, JP66.2, JP68.1
QWIIC_BUS17: J86.2, J87.2, JP70.2, JP72.1
QWIIC_BUS18: J91.2, J92.2, JP74.2, JP76.1
QWIIC_BUS19: J96.2, J97.2, JP78.2, JP80.1
QWIIC_BUS20: J101.2, J102.2, JP82.2, JP84.1
QWIIC_BUS21: J106.2, J107.2, JP86.2, JP88.1
QWIIC_BUS22: J111.2, J112.2, JP90.2, JP92.1
QWIIC_BUS23: J116.2, J117.2, JP94.2, JP96.1
QWIIC_BUS24: J121.2, J122.2, JP98.2, JP100.1
QWIIC_BUS25: J126.2, J127.2, JP102.2, JP104.1
QWIIC_BUS26: J131.2, J132.2, JP106.2, JP108.1
QWIIC_BUS27: J136.2, J137.2, JP110.2, JP112.1
QWIIC_BUS28: J141.2, J142.2, JP114.2, JP116.1
QWIIC_BUS29: J146.2, J147.2, JP118.2, JP120.1
SCL: J1.4, J2.4, J3.4, R2.1, U1.P11
SCL1: J6.4, J7.4, J8.4, R6.1, U2.P11
SCL2: J11.4, J12.4, J13.4, R10.1, U3.P11
SCL3: J16.4, J17.4, J18.4, R14.1, U4.P11
SCL4: J21.4, J22.4, J23.4, R18.1, U5.P11
SCL5: J26.4, J27.4, J28.4, R22.1, U6.P11
SCL6: J31.4, J32.4, J33.4, R26.1, U7.P11
SCL7: J36.4, J37.4, J38.4, R30.1, U8.P11
SCL8: J41.4, J42.4, J43.4, R34.1, U9.P11
SCL9: J46.4, J47.4, J48.4, R38.1, U10.P11
SCL10: J51.4, J52.4, J53.4, R42.1, U11.P11
SCL11: J56.4, J57.4, J58.4, R46.1, U12.P11
SCL12: J61.4, J62.4, J63.4, R50.1, U13.P11
SCL13: J66.4, J67.4, J68.4, R54.1, U14.P11
SCL14: J71.4, J72.4, J73.4, R58.1, U15.P11
SCL15: J76.4, J77.4, J78.4, R62.1, U16.P11
SCL16: J81.4, J82.4, J83.4, R66.1, U17.P11
SCL17: J86.4, J87.4, J88.4, R70.1, U18.P11
SCL18: J91.4, J92.4, J93.4, R74.1, U19.P11
SCL19: J96.4, J97.4, J98.4, R78.1, U20.P11
SCL20: J101.4, J102.4, J103.4, R82.1, U21.P11
SCL21: J106.4, J107.4, J108.4, R86.1, U22.P11
SCL22: J111.4, J112.4, J113.4, R90.1, U23.P11
SCL23: J116.4, J117.4, J118.4, R94.1, U24.P11
SCL24: J121.4, J122.4, J123.4, R98.1, U25.P11
SCL25: J126.4, J127.4, J128.4, R102.1, U26.P11
SCL26: J131.4, J132.4, J133.4, R106.1, U27.P11
SCL27: J136.4, J137.4, J138.4, R110.1, U28.P11
SCL28: J141.4, J142.4, J143.4, R114.1, U29.P11
SCL29: J146.4, J147.4, J148.4, R118.1, U30.P11
SDA: J1.3, J2.3, J3.3, R1.1, U1.P10
SDA1: J6.3, J7.3, J8.3, R5.1, U2.P10
SDA2: J11.3, J12.3, J13.3, R9.1, U3.P10
SDA3: J16.3, J17.3, J18.3, R13.1, U4.P10
SDA4: J21.3, J22.3, J23.3, R17.1, U5.P10
SDA5: J26.3, J27.3, J28.3, R21.1, U6.P10
SDA6: J31.3, J32.3, J33.3, R25.1, U7.P10
SDA7: J36.3, J37.3, J38.3, R29.1, U8.P10
SDA8: J41.3, J42.3, J43.3, R33.1, U9.P10
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

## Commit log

2020-11-10 Inital commit - Generic 1x1 Qwiic Board
    [Qwiic_Haptic_Driver_DA7280.brd, Qwiic_Haptic_Driver_DA7280.sch]
2020-11-10 Adds Da7280 footprint and symbol to library
    * Adds relevant datasheets
2020-11-11 Cleans up the Haptic Motor Driver Footprint and Device
    * Adds coin vibration motor
2020-11-11 Fully routed the board - still needs silk
    Minor changes to the DA7280:
    * symbol size was shortened.
    * Footprint was centered at 0,0
    [Qwiic_Haptic_Driver_DA7280.brd, Qwiic_Haptic_Driver_DA7280.sch]
2020-11-12 Adds silk to PTH headers, cleans up schematic
    [Qwiic_Haptic_Driver_DA7280.brd, Qwiic_Haptic_Driver_DA7280.sch]
2020-11-12 Updates PTH headers to PTH headers with no PROD_ID
    [Qwiic_Haptic_Driver_DA7280.brd, Qwiic_Haptic_Driver_DA7280.sch]
2020-11-12 Moves PTH interrupt closer to GND PTH hold and shifts all the GPI down.
    [Qwiic_Haptic_Driver_DA7280.brd, Qwiic_Haptic_Driver_DA7280.sch]
2020-11-19 Adds new package for the vibration motor - one that will go through the PCB
    * The new package has castellated leads to the part was rotated 180 degrees to the edge of the board.
    * Fixes interrupt silk to reflect active low
    [Qwiic_Haptic_Driver_DA7280.brd, Qwiic_Haptic_Driver_DA7280.sch]
2020-11-19 Updates SCL silk - updates LRA symbol by removing pin numbers
    [Qwiic_Haptic_Driver_DA7280.brd, Qwiic_Haptic_Driver_DA7280.sch]
2021-02-02 Flips the LRA motor 180, extends board to be 1.15 x 1 inches, adds 4.7iF decoupling capacitor
    * Gerbers in repo are out of date
    [Qwiic_Haptic_Driver_DA7280-Panel.brd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]
2021-02-03 Widens the power traces to .02" , rotates the GND,VCC, SDA, SCL header
    [Qwiic_Haptic_Driver_DA7280.brd]
2021-02-03 Approves two DRC errors
    [Qwiic_Haptic_Driver_DA7280.brd]
2021-02-11 Adds a jumper and plated through hole for separate VDDIO supply, adds silk for VDD
    * Changes power symbols to VDD and VDDIO in place of 3V3
    [Qwiic_Haptic_Driver_DA7280.brd, Qwiic_Haptic_Driver_DA7280.sch]
2021-02-12 Fixes some hidden airwires, approves some minor DRC errors
    [Qwiic_Haptic_Driver_DA7280.brd]
2021-02-18 Adds Jumpers for separating VDDIO from VDD and Qwiic bus voltage from the board
    * Updates measures
    * Adds OSHW and SparkFun logo to board
    * Adds text to jumpers in the schematic
    * Updates symbol to use short legs
    * Adds VDD and VDDIO range
    [Qwiic_Haptic_Driver_DA7280.brd, Qwiic_Haptic_Driver_DA7280.sch]
2021-02-18 Approves some minor DRC errors
    [Qwiic_Haptic_Driver_DA7280.brd]
2021-02-18 Adds second qwiic connecter to "qwiic bus" net so that the respective jumper can disconnect both
    * Adds some power symbols
    [Qwiic_Haptic_Driver_DA7280.brd, Qwiic_Haptic_Driver_DA7280.sch]
2021-02-18 Updates the PROD_ID on the vibration motor
    [Qwiic_Haptic_Driver_DA7280.brd, Qwiic_Haptic_Driver_DA7280.sch]
2021-02-19 Improves ground pour just a smidge, found better routing options when reviewing panel
    [Qwiic_Haptic_Driver_DA7280-Panel.GBL, Qwiic_Haptic_Driver_DA7280-Panel.GBP, Qwiic_Haptic_Driver_DA7280-Panel.GBS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]
2021-02-19 Adds new panel
    [Qwiic_Haptic_Driver_DA7280-Panel.GBL, Qwiic_Haptic_Driver_DA7280-Panel.GBP, Qwiic_Haptic_Driver_DA7280-Panel.GBS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]
2021-03-12 Removes incorrect gerbers from production file
    [Qwiic_Haptic_Driver_DA7280.GBL, Qwiic_Haptic_Driver_DA7280.GBO, Qwiic_Haptic_Driver_DA7280.GBP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]
2021-04-13 Adds a soldering jig for the LRA motor
    [Qwiic_Haptic_Driver_DA7280-Panel_SOLDERING_JIG.brd]

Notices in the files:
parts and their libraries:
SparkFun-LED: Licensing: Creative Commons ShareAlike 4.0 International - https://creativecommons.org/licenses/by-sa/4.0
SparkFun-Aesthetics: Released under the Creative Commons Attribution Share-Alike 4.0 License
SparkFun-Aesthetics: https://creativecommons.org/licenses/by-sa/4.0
